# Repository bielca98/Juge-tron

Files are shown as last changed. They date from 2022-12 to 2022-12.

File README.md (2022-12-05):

# Juge-tron

# Tabla de contenidos
<li>
<a href="#whatis"> ¿Qué es este proyecto? </a>
</li>

<li>
<a href="#req"> Requerimientos </a>
</li>

<li>
<a href="#docu"> Documentación </a>
</li>

<li>
<a href="#howtouse"> Cómo ejecutar la simulación </a>
</li>

<li>
<a href="#design" id="#design"> Diseño del robot </a>
 <ul>
  <li>
   <a href="#components"> Componentes </a>
  </li>
  <li>
   <a href="#esq3d"> Esquema 3D </a>
  </li>
  <li>
   <a href="#esqHW"> Esquema Hardware </a>
  </li> 
 </ul>
</li>

<li>
<a href="#software"> Arquitectura Software </a>
 <ul>
  <li>
  <a href="#VC"> Visión por computador </a>
  </li>
  <ul>
   <li>
    <a href="#detectObst"> Detector de obstáculos </a>
   </li>
   <li>
    <a href="#detectorConcr"> Detector concreto </a>
   </li>
   </ul>
  </ul>
 <ul>
 <li>
  <a href="#pathpl"> Path-Planning </a>
 </li>
 <li>
  <a href="#otrosSens"> Otros Sensores </a>
 </li>
 <li>
  <a href="#calcMov"> Cálculo de movimiento </a>
 </li>
 <li>
  <a href="#arduino"> Arduino </a>
 </li>
 </ul>
</li>

<li>
<a href="#sim"> Simulación </a>
</li>

<li>
<a href="#autores"> Autores </a>
</li>

<div id='whatis'/>

##  ¿Qué es este proyecto?
Este es el repositorio de un proyecto que trata de un robot en forma de bola que tiene como función jugar con las mascotas huyendo de ellas. Para realizar este propósito, el robot contará con una cámara con la cual, a través de visión por computador, será capaz de visualizar al animal y su entorno para así poder actuar con cierta personalidad. 
El robot se moverá debido a la fricción ejercida por unas ruedas internas contra la carcasa de la bola, y los elementos del interior se mantendrán estables debido a un peso que ejercerá de centro de masas.

<div id='req'/>

## Requerimientos
Para ejecutar la simulación hacen falta las siguientes dependencias de python:
```
pip install numpy, opencv-python, tensorflow
```
También se requiere tener instalado el simulador Webots. 
 
<div id='docu'/>

## Documentación
Los siguientes proyectos han servido como referencia e inspiración:
https://www.hindawi.com/journals/complexity/2019/7543969/
https://www.sciencedirect.com/science/article/pii/S0307904X14006015
https://github.com/tensorflow/models/blob/master/research/object_detection/colab_tutorials/object_detection_tutorial.ipynb
https://nanonets.com/blog/optical-flow/

<div id='howtouse'/>

## Cómo ejecutar la simulación
1. Clonar el repositorio
2. Instalar PyTorch desde https://pytorch.org/, elegir CUDA 11.1 o mayor si se desea utilizar la GPU. 
3. Instalar las siguientes dependencias
```
pip install -U --pre tensorflow=="2.*"
pip install tf_slim
pip install -r requirements.txt
```
4. Dirigirse a la carpeta "/Reconocimiento de imágenes" y ejecutar los siguientes comandos:

``` 
powershell
cd research/
protoc object_detection/protos/*.proto --python_out=.
pip install .
```
5. Abrir haciendo doble click uno de los escenarios presentes en /RLP_Sim/worlds

<div id='design'/>

## Diseño del robot 

En esta carpeta se incluye el diseño que tendrá el robot.

<div id='components'/>

### Componentes
Los componentes Hardware utilizados serán los siguientes:

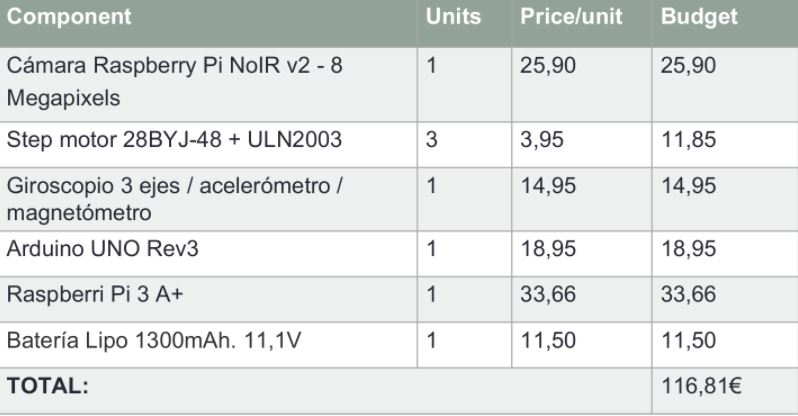
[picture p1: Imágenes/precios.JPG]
components


El tamaño de cada componente se incluye en la siguiente tabla:

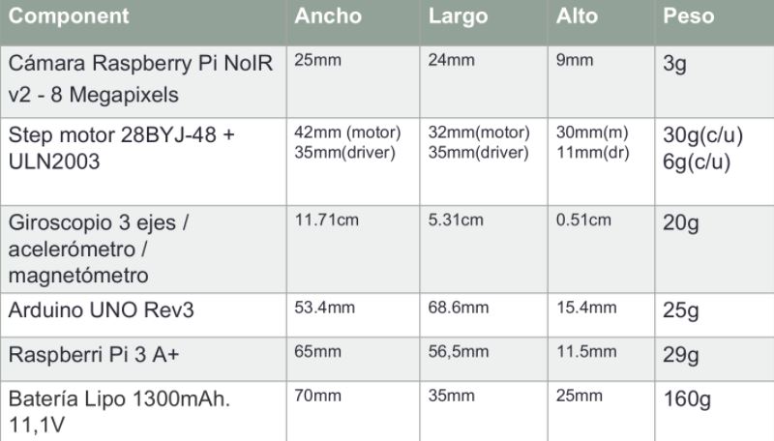
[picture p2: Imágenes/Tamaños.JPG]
tamany


<div id='esq3D'/>

### Esquema 3D
El esquema básico dentro de la bola se compone de una base cilíndrica, sobre la que se colocarán los componentes hardware necesarios, tres ruedas que harán girar la carcasa de la bola mediante la fricción que ejerzan sobre ella, y tres varitas que unan las ruedas a la base. Este esquema se muestra en la siguiente imagen:

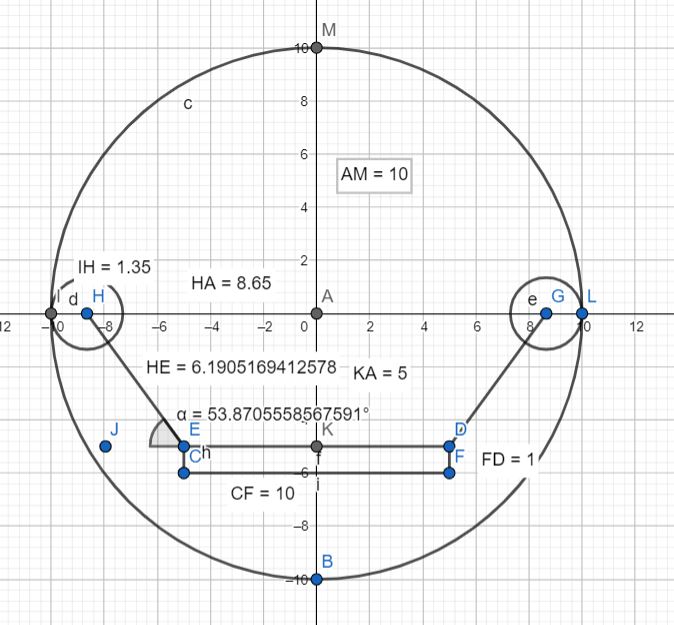
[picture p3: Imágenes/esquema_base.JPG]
base


las piezas aquí mostradas se obtendrán mediante impresión 3D. Las medidas, colocación y ángulos relevantes de estas se indican en el esquema. El diseño 3D de las varitas incluye un pequeño soporte para poder pegarlas a la base con pegamento, un espacio para poder colocar las ruedas, y un agujero con una pieza que permite fijar las ruedas a la varita.

Debajo de la base se pegará un cilindro. Contendrá un peso que ejercerá como centro de masas para estabilizar el robot internamente. Este cilindro también se obtendrá con impresión 3D.

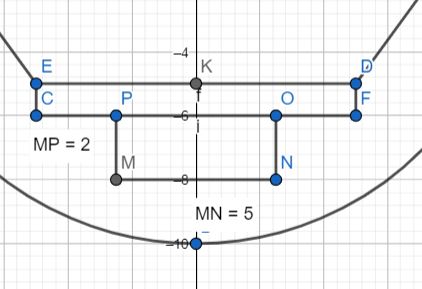
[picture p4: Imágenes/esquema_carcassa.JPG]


Finalmente, encima de la base se colocarán los diferentes componentes Hardware de manera estratégica.

Las ruedas se conectarán a los motores mediante un sistema de poleas. El diseño de las piezas 3D se incluye en la carpeta piezas, y en el archivo Esquema3d.dwg se ha incluido un modelo 3D del esquema de colocación de las piezas que aquí se ha explicado.

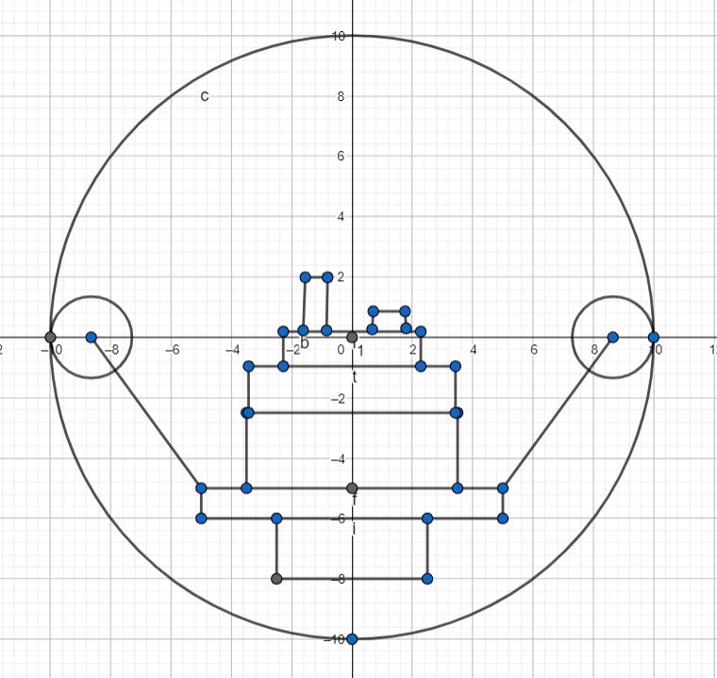
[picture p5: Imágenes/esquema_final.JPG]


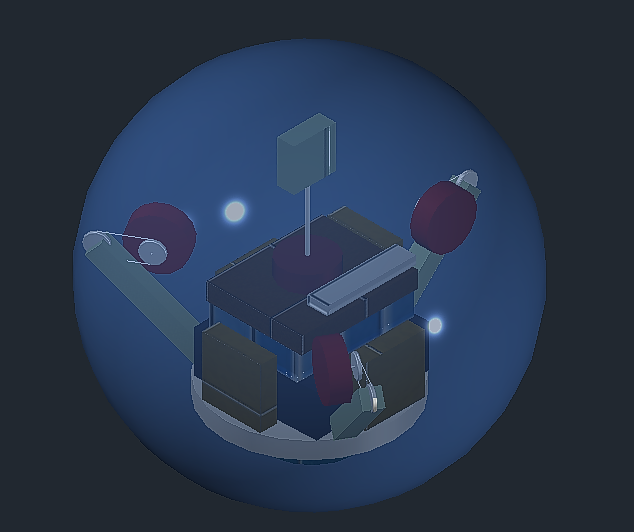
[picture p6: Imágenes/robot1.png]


<div id='esqHW'/>

### Esquema Hardware
El esquema de conexión entre los diferentes componentes hardware es el siguiente

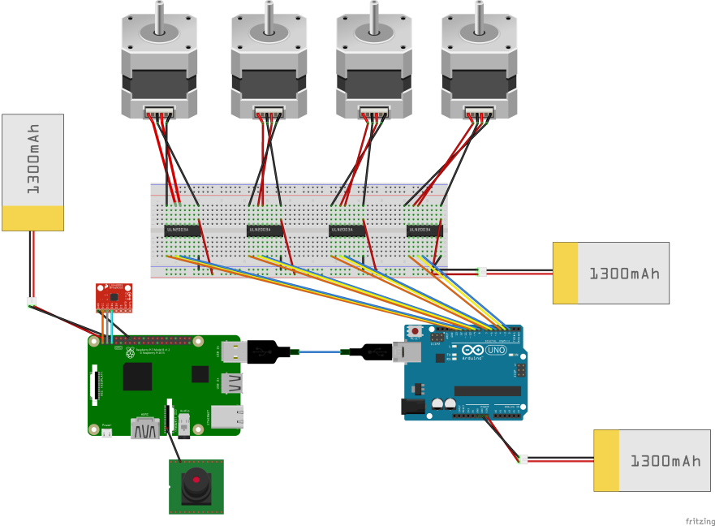
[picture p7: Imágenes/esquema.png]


<div id='software'/>

## Arquitectura Software
Se han identificado los diferentes módulos software

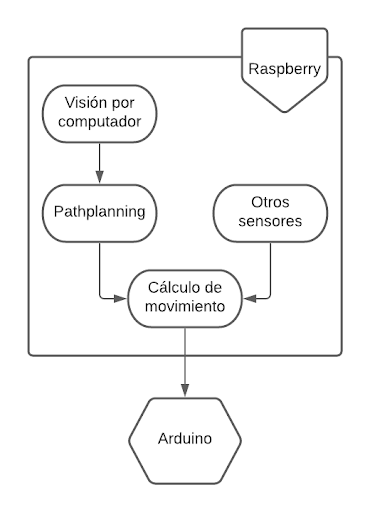
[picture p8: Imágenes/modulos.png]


<div id='VC'/>

### Visión por computador

Este módulo será el encargado de interpretar las imágenes que entren como input desde la cámara. Aquí se efectuará la obtención de datos a partir de las imágenes.
 
Se hará uso de un modelo entrenado de redes neuronales capaz de reconocer al animal doméstico y, mediante procesamiento de imagen, de posicionarlo en el espacio. Además reconocerá también obstáculos que haya en el camino para, una vez identificado todo, pasar esta información al módulo de pathplanning.

Para lograrlo, se hará uso de las librerías Python OpenCV (para la captación y procesamiento de la imagen) y Keras (para el uso de modelos de inteligencia artificial). 
Este módulo se puede dividir en dos detectores diferentes, el detector de obstáculos y el detector concreto.

<div id='detectObst'/>

#### Detector de obstáculos
El detector de obstáculos tendrá la función de identificar obstáculos que el robot pueda encontrar en su camino y extraer información de estos, como puede ser la distancia o la posición de estos.

Se ha optado por un enfoque en el que se ha usado un algoritmo de Dense Optical Flow. Así pues, el algoritmo de visión del MVP aplica el algoritmo de Optical Flow sobre el frame anterior y el actual y aprovecha las magnitudes devueltas a las que aplica un threshold y, por último, un closing para eliminar posible ruido y unir algunas partes que pudieran quedar sueltas. La máscara resultante es la que se devolverá y se usará para el pathplanning. Este proceso queda reflejado en el siguiente diagrama.

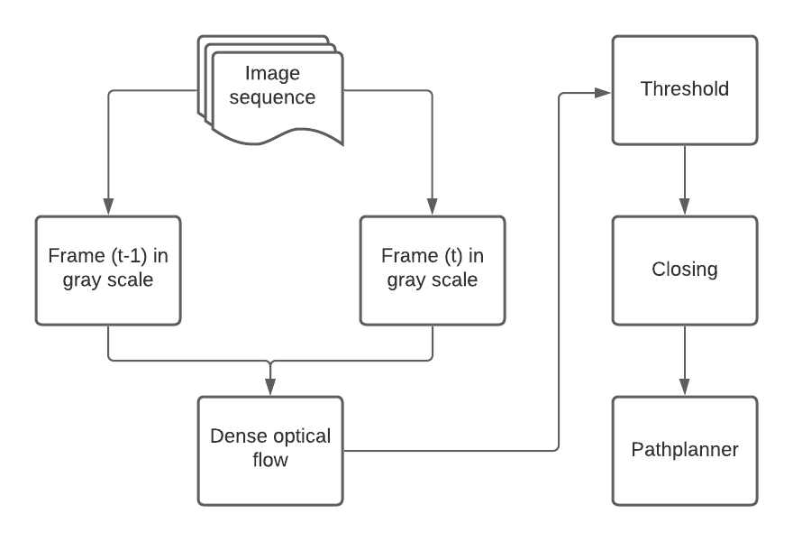
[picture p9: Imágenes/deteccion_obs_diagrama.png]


Por otro lado, en la siguiente imagen se puede observar un ejemplo de máscara devuelta.
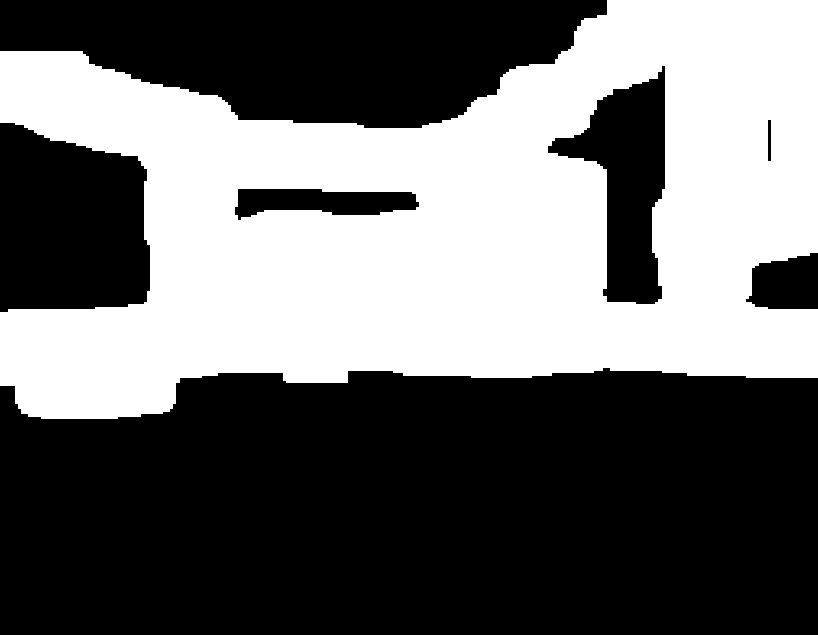
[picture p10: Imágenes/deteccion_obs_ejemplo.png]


<div id='detectorConcr'/>

#### Detector concreto
El detector concreto se encargará de identificar objetos clave, en nuestro caso la mascota de la que tendrá que huir. Igual que el detector de obstáculos, también devolverá información de estos objetos, en este caso, la bounding box.
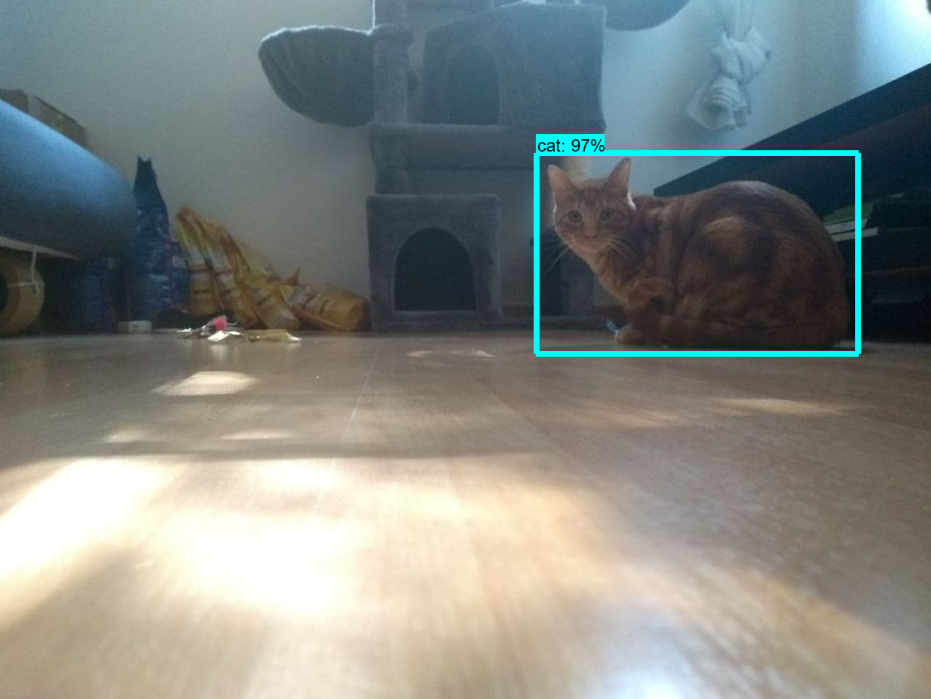
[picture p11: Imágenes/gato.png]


<div id='pathpl'/>

### Path-planning
Este módulo será el que se encargue de procesar el mapa generado por el módulo de visión por computador, teniendo en cuenta la localización de la mascota y de los obstáculos. Trazará una ruta que será ejecutada mediante el movimiento de los motores internos del robot. 

Se seguirá una estrategia greedy para trazar una ruta puesto que no se contará con el mapeo del entorno. El algoritmo trabajará únicamente con la información recibida por el módulo de visión, con la que podrá hacer una mínima planificación de una posible ruta a seguir, aunque esta podrá ser modificada mientras se recorre (debido a imprevistos).

El algoritmo ha sido programado por el equipo íntegramente, tomando como referencia algoritmos de búsqueda local.

En definitiva, se ha definido una máquina de estados finitos que define la personalidad del robot.

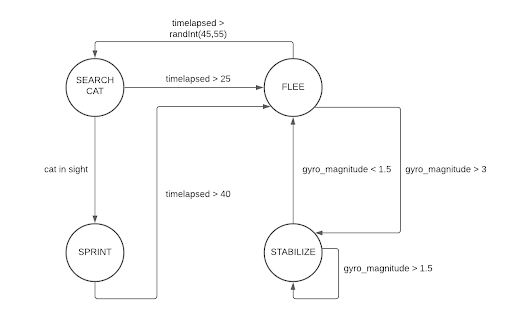
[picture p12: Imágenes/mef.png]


La máquina cuenta con 4 estados: FLEE, STABILIZE, SEARCH CAT y SPRINT. En el primer estado, el robot correrá libremente esquivando obstáculos y paredes durante unos segundos. Una vez transcurridos estos segundos, se parará para buscar al gato (estado SEARCH CAT). Más adelante se explicará en profundidad la parte fundamental del algoritmo de esquiva de obstáculos. El segundo estado para los motores y espera a que las lecturas del giroscopio se normalicen, para ello se calcula la la magnitud del vector de lectura y se compara con un threshold (tal y como se puede observar en la imagen anterior). El tercer estado da la orden de parar motores y rota la cámara hasta dar con el gato. Si este no estuviera en su rango de visión y transcurridos unos segundos el robot volvería al estado de FLEE. En caso contrario, entra en estado de SPRINT, el cual ejecuta el mismo algoritmo que el estado FLEE pero multiplicando por un factor la velocidad de movimiento y de rotación emulando una reacción exagerada. De esta manera, el robot adquiere una personalidad que llamará la atención de los gatos y la mantendrá.

El algoritmo de esquiva de obstáculos toma la máscara devuelta por el módulo de visión y crea un vector con el índice máximo en el que hay un valor diferente de 0 de cada columna. Este vector simboliza una línea del horizonte. Entonces, hace un sumatorio a partir de cada valor del vector ponderado por la distancia respecto al límite superior de la imagen y al centro en el eje horizontal. El resultado de este valor marcará en qué dirección y con qué velocidad deberá girar el robot. El algoritmo también calcula la velocidad de movimiento a partir de la diferencia del ancho de la imagen entre la media de los valores del vector y un threshold. De esta manera, cuanto más cercana al robot sea la línea del horizonte, más despacio irá para poder maniobrar mejor.

<div id='otrosSens'/>

### Otros sensores
Este módulo controlará los datos del giroscopio/acelerómetro y los traducirá a órdenes sobre los tres motores internos. Los datos extraídos serán trasladados a información necesaria para que el robot pueda mantenerse erguido, cosa que se considera de fundamental importancia ya que así la cámara podrá extraer datos más precisos.

Los sensores estarán conectados a la raspberry, en la cual se usará la librería mpu6050-raspberrypi 1.1 para leer los valores del giroscopio/acelerómetro.

<div id='calcMov'/>

### Cálculo de movimiento
A partir de la dirección recibida por el módulo de pathplanning y la información de los demás sensores, este módulo calculará con precisión el próximo movimiento y fuerza a aplicar en los motores. Este buscará, en la medida de lo posible, seguir el camino trazado por el pathplanner y mantener estable la estructura interna del robot.

<div id='arduino'/>

### Arduino

Este módulo hará de actuador y enviará las señales a los motores mediante la librería stepper.

<div id='sim'/>

## Simulación

La simulación se ha llevado a cabo en el simulador Webots, dado que se trata de un simulador con un motor de físicas suficientemente complejo como para simular el robot.  El primer objetivo ha sido crear el modelo 3D y modelar las funciones de movimiento del robot a partir del movimiento de las ruedas, teniendo en cuenta todos los factores físicos  posibles (inercia, fricción, gravedad, etc.) tal y como ocurriría en la vida real.

Posteriormente, se ha generardo un entorno realista basado en una vivienda amueblada donde el modelo definido ha sido testeado. Así, se pueden ver las interacciones con los obstáculos estáticos y, también,  con los dinámicos.  La simulación mostrará en todo momento  un punto de vista desde el que se pueda ver la bola por la parte de atrás.

El modelo del robot simulado cuenta con una carcasa, 3 motores rotacionales y un cilindro que actúa como centro de masas. El robot se puede controlar mediante el teclado enviando instrucciones directamente a cada uno de los motores con los que cuenta, o bien de manera automática.

Se ha escrito un plugin para el simulador que calcula la velocidad angular de la esfera a partir de las velocidades de las tres ruedas utilizando la siguiente fórmula.

base

Finalmente, se ha añadido un gato montado en un robot móvil que se irá moviendo por el entorno para que el juguetron pueda detectarlo.

Se puede ver un vídeo que muestra la simulación en el siguiente link
https://www.youtube.com/watch?v=o8pFeoxQk68

<div id='autores'/>

## Autores
Iván Lorenzo Alcaina

Pablo Chen

Biel Castaño Segade

Sergi Masip Cabeza

Este proyecto se ha realizado para la asignatura Robótica, Lenguaje y Programación, de la mención de computación de Ingenieria informática por la Universidad Autónoma de Barcelona.

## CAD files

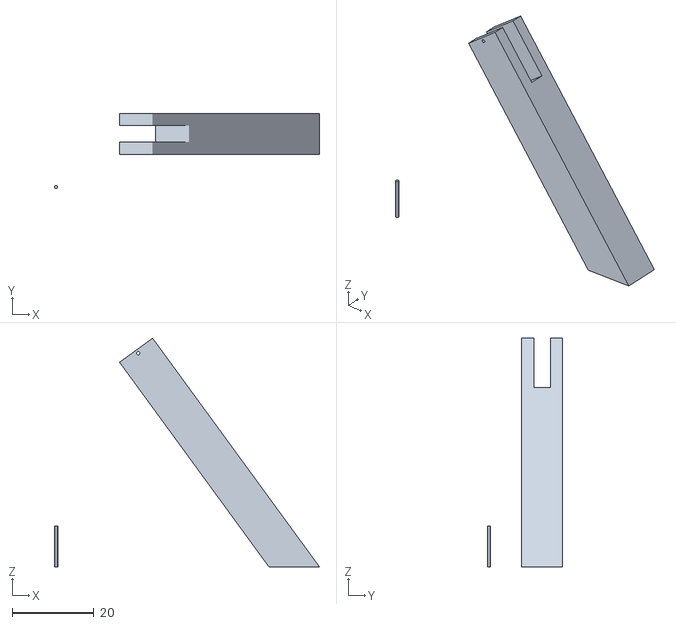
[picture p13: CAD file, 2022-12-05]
Diseño/Piezas_3D/Soporte para las ruedas.stl
64.8 x 18.4 x 55.9

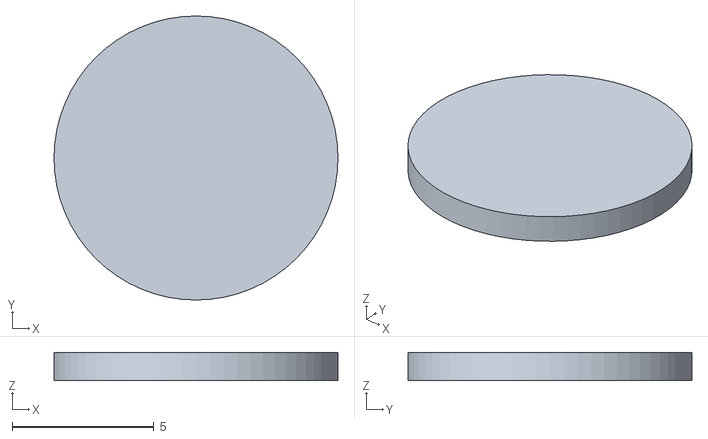
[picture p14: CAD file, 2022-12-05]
Diseño/Piezas_3D/Soporte de la estructura interna.stl
10.0 x 10.0 x 1.00

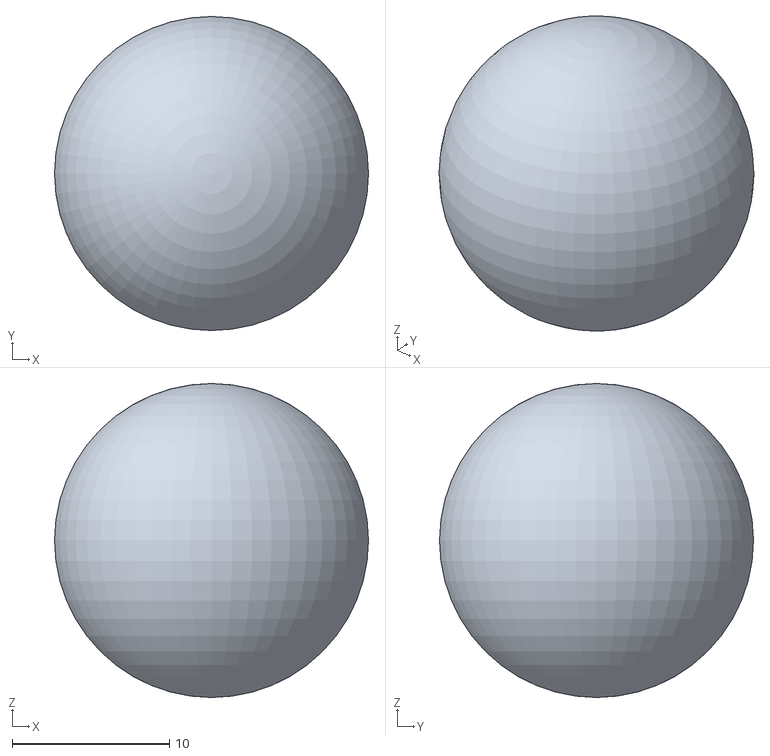
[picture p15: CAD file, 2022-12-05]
Diseño/Piezas_3D/Carcasa esférica.stl
20.0 x 20.0 x 20.0

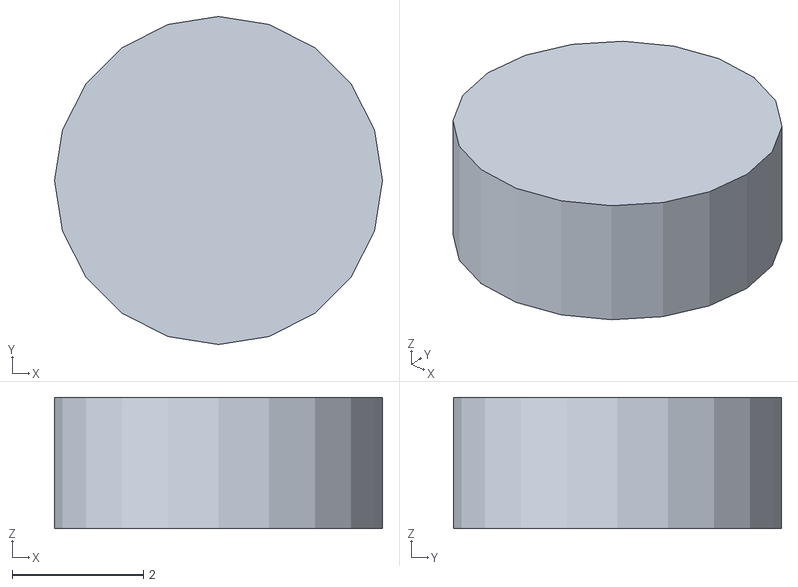
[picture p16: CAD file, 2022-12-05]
Diseño/Piezas_3D/Cilindro (centro de masas).stl
5.00 x 5.00 x 2.00

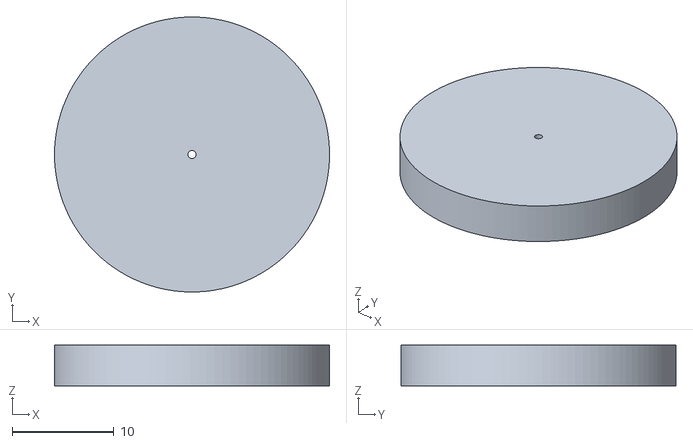
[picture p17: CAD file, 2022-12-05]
Diseño/Piezas_3D/Rueda.stl
27.0 x 27.0 x 4.00

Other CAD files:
Diseño/Esquema.dwg

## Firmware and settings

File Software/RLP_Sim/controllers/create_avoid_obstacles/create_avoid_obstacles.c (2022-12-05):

/*
 * Copyright 1996-2020 Cyberbotics Ltd.
 *
 * Licensed under the Apache License, Version 2.0 (the "License");
 * you may not use this file except in compliance with the License.
 * You may obtain a copy of the License at
 *
 *     http://www.apache.org/licenses/LICENSE-2.0
 *
 * Unless required by applicable law or agreed to in writing, software
 * distributed under the License is distributed on an "AS IS" BASIS,
 * WITHOUT WARRANTIES OR CONDITIONS OF ANY KIND, either express or implied.
 * See the License for the specific language governing permissions and
 * limitations under the License.
 */

/*
 * Description:  Default controller of the iRobot Create robot
 */

/* include headers */
#include <math.h>
#include <stdio.h>
#include <stdlib.h>
#include <time.h>

#include <webots/distance_sensor.h>
#include <webots/led.h>
#include <webots/motor.h>
#include <webots/position_sensor.h>
#include <webots/receiver.h>
#include <webots/robot.h>
#include <webots/touch_sensor.h>

/* device stuff */
#define BUMPERS_NUMBER 2
#define BUMPER_LEFT 0
#define BUMPER_RIGHT 1
static WbDeviceTag bumpers[BUMPERS_NUMBER];
static const char *bumpers_name[BUMPERS_NUMBER] = {"bumper_left", "bumper_right"};

#define CLIFF_SENSORS_NUMBER 4
#define CLIFF_SENSOR_LEFT 0
#define CLIFF_SENSOR_FRONT_LEFT 1
#define CLIFF_SENSOR_FRONT_RIGHT 2
#define CLIFF_SENSOR_RIGHT 3
static WbDeviceTag cliff_sensors[CLIFF_SENSORS_NUMBER];
static const char *cliff_sensors_name[CLIFF_SENSORS_NUMBER] = {"cliff_left", "cliff_front_left", "cliff_front_right",
                                                               "cliff_right"};

#define LEDS_NUMBER 3
#define LED_ON 0
#define LED_PLAY 1
#define LED_STEP 2
static WbDeviceTag leds[LEDS_NUMBER];
static const char *leds_name[LEDS_NUMBER] = {"led_on", "led_play", "led_step"};

static WbDeviceTag receiver;
static const char *receiver_name = "receiver";

WbDeviceTag left_motor, right_motor, left_position_sensor, right_position_sensor;

/* Misc Stuff */
#define MAX_SPEED 16
#define NULL_SPEED 0
#define HALF_SPEED 8
#define MIN_SPEED -16

#define WHEEL_RADIUS 0.031
#define AXLE_LENGTH 0.271756
#define ENCODER_RESOLUTION 507.9188

/* helper functions */
static int get_time_step() {
  static int time_step = -1;
  if (time_step == -1)
    time_step = (int)wb_robot_get_basic_time_step();
  return time_step;
}

static void step() {
  if (wb_robot_step(get_time_step()) == -1) {
    wb_robot_cleanup();
    exit(EXIT_SUCCESS);
  }
}

static void init_devices() {
  int i;

  receiver = wb_robot_get_device(receiver_name);
  wb_receiver_enable(receiver, get_time_step());

  for (i = 0; i < LEDS_NUMBER; i++)
    leds[i] = wb_robot_get_device(leds_name[i]);

  for (i = 0; i < BUMPERS_NUMBER; i++) {
    bumpers[i] = wb_robot_get_device(bumpers_name[i]);
    wb_touch_sensor_enable(bumpers[i], get_time_step());
  }

  for (i = 0; i < CLIFF_SENSORS_NUMBER; i++) {
    cliff_sensors[i] = wb_robot_get_device(cliff_sensors_name[i]);
    wb_distance_sensor_enable(cliff_sensors[i], get_time_step());
  }

  left_motor = wb_robot_get_device("left wheel motor");
  right_motor = wb_robot_get_device("right wheel motor");
  wb_motor_set_position(left_motor, INFINITY);
  wb_motor_set_position(right_motor, INFINITY);
  wb_motor_set_velocity(left_motor, 0.0);
  wb_motor_set_velocity(right_motor, 0.0);

  left_position_sensor = wb_robot_get_device("left wheel sensor");
  right_position_sensor = wb_robot_get_device("right wheel sensor");
  wb_position_sensor_enable(left_position_sensor, get_time_step());
  wb_position_sensor_enable(right_position_sensor, get_time_step());
}

static bool is_there_a_collision_at_left() {
  return (wb_touch_sensor_get_value(bumpers[BUMPER_LEFT]) != 0.0);
}

static bool is_there_a_collision_at_right() {
  return (wb_touch_sensor_get_value(bumpers[BUMPER_RIGHT]) != 0.0);
}

static void fflush_ir_receiver() {
  while (wb_receiver_get_queue_length(receiver) > 0)
    wb_receiver_next_packet(receiver);
}

static bool is_there_a_virtual_wall() {
  return (wb_receiver_get_queue_length(receiver) > 0);
}

static bool is_there_a_cliff_at_left() {
  return (wb_distance_sensor_get_value(cliff_sensors[CLIFF_SENSOR_LEFT]) < 100.0 ||
          wb_distance_sensor_get_value(cliff_sensors[CLIFF_SENSOR_FRONT_LEFT]) < 100.0);
}

static bool is_there_a_cliff_at_right() {
  return (wb_distance_sensor_get_value(cliff_sensors[CLIFF_SENSOR_RIGHT]) < 100.0 ||
          wb_distance_sensor_get_value(cliff_sensors[CLIFF_SENSOR_FRONT_RIGHT]) < 100.0);
}

static bool is_there_a_cliff_at_front() {
  return (wb_distance_sensor_get_value(cliff_sensors[CLIFF_SENSOR_FRONT_LEFT]) < 100.0 ||
          wb_distance_sensor_get_value(cliff_sensors[CLIFF_SENSOR_FRONT_RIGHT]) < 100.0);
}

static void go_forward() {
  wb_motor_set_velocity(left_motor, MAX_SPEED);
  wb_motor_set_velocity(right_motor, MAX_SPEED);
}

static void go_backward() {
  wb_motor_set_velocity(left_motor, -HALF_SPEED);
  wb_motor_set_velocity(right_motor, -HALF_SPEED);
}

static void stop() {
  wb_motor_set_velocity(left_motor, -NULL_SPEED);
  wb_motor_set_velocity(right_motor, -NULL_SPEED);
}

static void passive_wait(double sec) {
  double start_time = wb_robot_get_time();
  do {
    step();
  } while (start_time + sec > wb_robot_get_time());
}

static double randdouble() {
  return rand() / ((double)RAND_MAX + 1);
}

static void turn(double angle) {
  stop();
  double l_offset = wb_position_sensor_get_value(left_position_sensor);
  double r_offset = wb_position_sensor_get_value(right_position_sensor);
  step();
  double neg = (angle < 0.0) ? -1.0 : 1.0;
  wb_motor_set_velocity(left_motor, neg * HALF_SPEED);
  wb_motor_set_velocity(right_motor, -neg * HALF_SPEED);
  double orientation;
  do {
    double l = wb_position_sensor_get_value(left_position_sensor) - l_offset;
    double r = wb_position_sensor_get_value(right_position_sensor) - r_offset;
    double dl = l * WHEEL_RADIUS;                 // distance covered by left wheel in meter
    double dr = r * WHEEL_RADIUS;                 // distance covered by right wheel in meter
    orientation = neg * (dl - dr) / AXLE_LENGTH;  // delta orientation in radian
    step();
  } while (orientation < neg * angle);
  stop();
  step();
}

/* main */
int main(int argc, char **argv) {
  wb_robot_init();

  printf("Default controller of the iRobot Create robot started...\n");

  init_devices();
  srand(time(NULL));

  wb_led_set(leds[LED_ON], true);
  passive_wait(0.5);

  while (true) {
    if (is_there_a_virtual_wall()) {
      printf("Virtual wall detected\n");
      turn(M_PI);
    } else if (is_there_a_collision_at_left() || is_there_a_cliff_at_left()) {
      printf("Left obstacle detected\n");
      go_backward();
      passive_wait(0.5);
      turn(M_PI * randdouble());
    } else if (is_there_a_collision_at_right() || is_there_a_cliff_at_right() || is_there_a_cliff_at_front()) {
      printf("Right obstacle detected\n");
      go_backward();
      passive_wait(0.5);
      turn(-M_PI * randdouble());
    } else
      go_forward();
    fflush_ir_receiver();
    step();
  };

  return EXIT_SUCCESS;
}
